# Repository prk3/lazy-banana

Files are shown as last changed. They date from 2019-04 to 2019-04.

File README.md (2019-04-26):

# About
Arduino Nano based controller for IKEA Bekant desk. Allows for manual height control, saving positions and auto height adjustment with a press of a button.

# Schematic
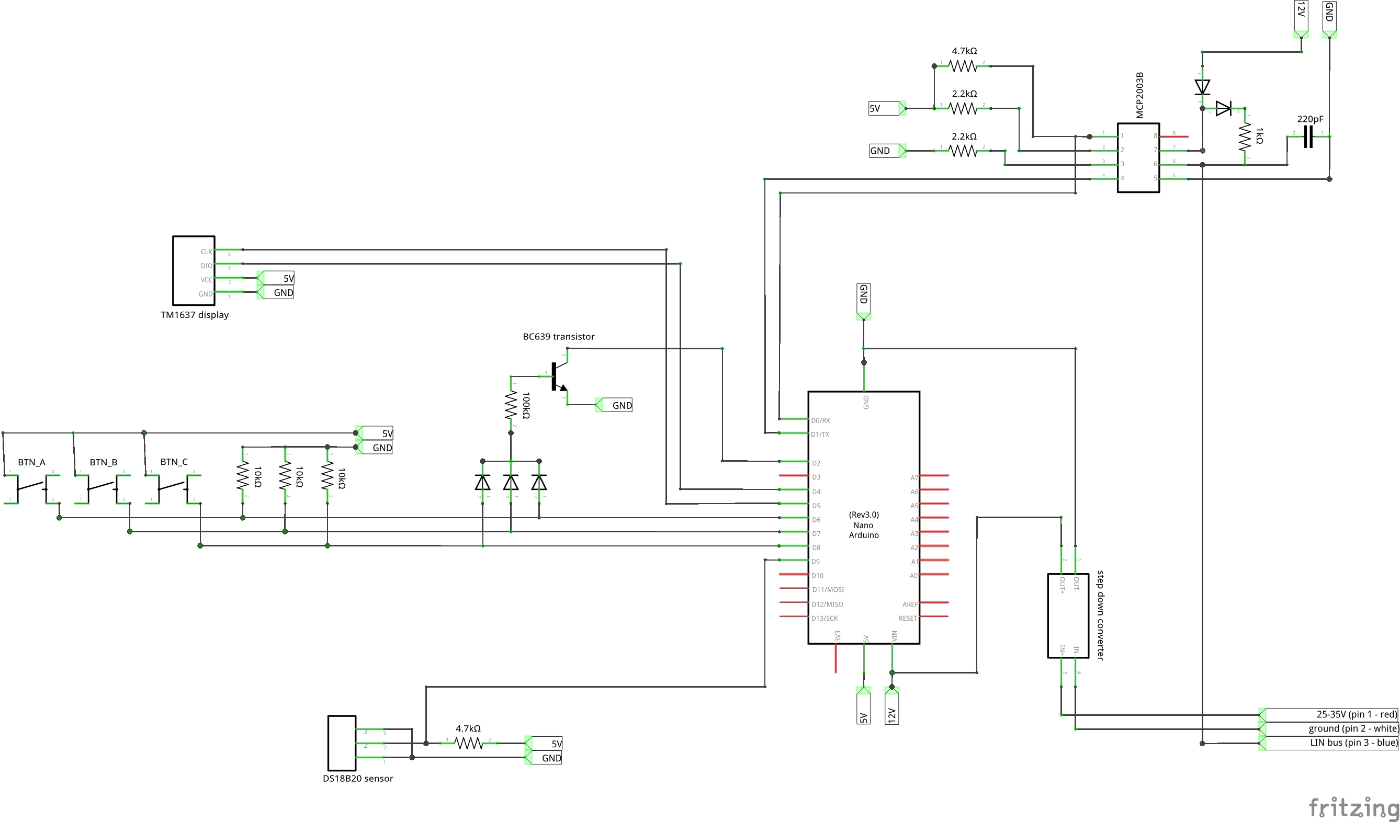
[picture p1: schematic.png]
Schematic

This schematic is a mix of trainman419's work, gcormier's improvements and my poor electronics skills. Please refer to the original in case you're uncertain about my schematic.

# Parts
| name | amount |
| --- | --- |
| Arduino nano clone - Atmega328, 16MHz, 5V | 1 |
| Step down converter LM2596S max 35V | 1 |
| 4-digit 7 segment display TM1637 | 1 |
| LIN interface/transceiver MCP2003B | 1 |
| temperature sensor DS18B20 | 1 |
| transistor BC639 | 1 |
| capacitor 220pF | 1 |
| diode 1N4148 | 5 |
| resistor 100k | 1 |
| resistor 10k | 3 |
| resistor 4.7k | 2 |
| resistor 2.2k | 2 |
| resistor 1k | 1 |

# Interface
Before testing auto-move, please factory reset the controller to initialize presets in EEPROM. You can do it by holding all three buttons on home screen.

- **SLEEP SCREEN**: Controller switches to this state after some time (15s by default) of inactivity. Press any button to wake up the controller and go to **home screen**.

- **HOME SCREEN**: Shows current height. Pressing buttons A-C will move desk to corresponding preset (**auto move screen**). Holding button A will redirect to **temperature screen**. Holding buttons B or C will redirect to **manual move screen**. Holding all three buttons will factory reset height presets.

- **TEMPERATURE SCREEN**: Shows temperature read from the Dallas sensor. Press any button to exit.

- **AUTO MOVE SCREEN**: Moves the desk to saved position. Press any button to cancel.

- **MANUAL MOVE SCREEN**: Holding B moves desk down, holding C moves desk up. Press button A to exit. Hold button A to save position (**save position screen**).

- **SAVE POSITION SCREEN**: Press button A, B or C to save position to preset 1, 2 or 3. Hold any button to cancel. 

# Code
Each part of controller's functionality is separated into `.cpp` + `.h` pair. All modules are then imported in `main.cpp` and used in a big state machine. Every state has it's id, initialization procedure and a handler (called every 50ms), which reacts to IO changes, performs some actions and redirects to a different state if needed.

All pins are configurable via const variables at the top of header files. Keep in mind that buttons work in INPUT mode and wake pin works in INPUT_PULLUP mode.

The code has been written in vscode with PlatformIO plugin. To make it work with Arduino IDE, move all files from `include`, `src` and `lib/gcormier_megadesk` to one folder named `main` and rename `main.cpp` file to `main.ino`. Make sure you have all dependencies installed.

# Dependencies
This project uses the following Arduino libraries:
1. OneWire - [https://github.com/PaulStoffregen/OneWire](https://github.com/PaulStoffregen/OneWire)
2. DallasTemperature - [https://github.com/milesburton/Arduino-Temperature-Control-Library.git](https://github.com/milesburton/Arduino-Temperature-Control-Library.git)
3. TM1637 [https://github.com/avishorp/TM1637.git](https://github.com/avishorp/TM1637.git)

# TODO
1. Add photos of the controller.
2. Model a case and 3d print it.
3. Record a demo.

# Issues
1. Auto move algorithm emulates UP/DOWN button pressing to reach target height. A better solution would be to keep desk in fine movement mode when it's close to target and slowly approach desired position.
2. Auto move algorithm isn't aware of desk's velocity. For this reason the desk refuses to move between presets that are very close to each other (controller thinks that desk is at full speed and would overshoot the target, thus it doesn't move at all).
3. Motors gradually slow down near min and max heights. This isn't handled by the controller and auto move undershoots targets near min and max.

# Credit
Big thanks to:
1. robin7331([IKEA-Hackant](https://github.com/robin7331/IKEA-Hackant/) project) for inspiring video and detailed explanation of desk's internals
2. trainman419 ([bekant](https://github.com/trainman419/bekant) project) for reproducing behavior of stock controller on Arduino
3. gcormier ([megadesk](https://github.com/gcormier/megadesk) project) for improvements to trainman419's schematic and code

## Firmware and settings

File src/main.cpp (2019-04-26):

#include <Arduino.h>
#include "buttons.h"
#include "display.h"
#include "temperature.h"
#include "desk.h"
#include "memory.h"
#include "state.h"
#include "sleep.h"

/**
 * Time after which controller goes to sleep.
 */
const uint16_t SLEEP_AFTER_S = 15;

unsigned long lastActivityTime = 0;

/**
 * The list of all program states.
 * It's a classic enum, because we want to avoid type errors.
 * ("states.h" doesn't know what states we'll have in the app)
 */
enum S: StateIdentifier {
    MAIN,
    AUTO_MOVE,
    MANUAL_MOVE,
    PRESET_CHOICE,
    PRESET_SAVE,
    FACTORY_RESET,
    TEMPERATURE,
    SLEEP,
};


// Each state requring data persistant across updates has it's own object.

struct {
    uint8_t preset = 0;
    uint16_t targetHeight = 0;
    bool forceStop = false;
    uint8_t finishedCount = 0;
} autoMoveData;

struct {
    uint8_t frame;
} infoStateData;

struct {
    uint8_t preset = 0;
} presetSaveData;

/**
 * Here we define how each state is initialized and handled in loop.
 */
const State states[] = {
    State {
        S::MAIN,
        []() {
            clearDisplayBuffer();
            drawIntegerInDisplayBuffer(getDeskHeight());
            sendBufferToDisplay();
        },
        [](StateChanger& changeState) {
            if (BTN_A.wasUnpressed()) {
                autoMoveData.preset = 0;
                return changeState(S::AUTO_MOVE);
            }
            if (BTN_B.wasUnpressed()) {
                autoMoveData.preset = 1;
                return changeState(S::AUTO_MOVE);
            }
            if (BTN_C.wasUnpressed()) {
                autoMoveData.preset = 2;
                return changeState(S::AUTO_MOVE);
            }

            if (!BTN_A.isPressed() && (BTN_B.wasHeld() || BTN_C.wasHeld())) {
                return changeState(S::MANUAL_MOVE, false);
            }

            if (BTN_A.wasHeld()) {
                if (BTN_B.isPressed() && BTN_C.isPressed()) {
                    return changeState(S::FACTORY_RESET);
                }

                return changeState(S::TEMPERATURE);
            }
        },
    },
    State {
        S::AUTO_MOVE,
        []() {
            autoMoveData.targetHeight = readPreset(autoMoveData.preset);
            autoMoveData.forceStop = false;
            autoMoveData.finishedCount = 0;
        },
        [](StateChanger& changeState) {
            clearDisplayBuffer();
            drawIntegerInDisplayBuffer(getDeskHeight());
            setColonInDisplayBuffer(true);
            sendBufferToDisplay();

            if (BTN_A.wasPressed() || BTN_B.wasPressed() || BTN_C.wasPressed()) {
                autoMoveData.forceStop = true;
            }

            // stops motors like if a button on the original controller was unpressed
            if (autoMoveData.forceStop) {
                if (!isDeskMoving()) {
                    return changeState(S::MAIN);
                }
                manualMoveLoop(ManualCommand::NONE);
            } else {
                // exit when "finished" reported 3 times
                if (!isDeskMoving() && ++autoMoveData.finishedCount > 3) {
                    return changeState(S::MAIN);
                }
                autoMoveLoop(autoMoveData.targetHeight);
            }
        },
    },
    State {
        S::MANUAL_MOVE,
        []() {},
        [](StateChanger& changeState) {
            clearDisplayBuffer();
            drawIntegerInDisplayBuffer(getDeskHeight());
            setColonInDisplayBuffer(true);
            sendBufferToDisplay();

            // change state only if desk is not moving
            if (!isDeskMoving()) {
                if (BTN_A.wasUnpressed()) {
                    return changeState(S::MAIN);
                }

                if (BTN_A.wasHeld()) {
                    return changeState(S::PRESET_CHOICE);
                }
            }

            if (!BTN_A.isPressed() && BTN_B.isPressed()  && !BTN_C.isPressed()) {
                manualMoveLoop(ManualCommand::DOWN);
            }
            else if (!BTN_A.isPressed() && !BTN_B.isPressed() && BTN_C.isPressed()) {
                manualMoveLoop(ManualCommand::UP);
            }
            else {
                manualMoveLoop(ManualCommand::NONE);
            }
        },
    },
    State {
        S::PRESET_CHOICE,
        []() {
            clearDisplayBuffer();
            drawIntegerInDisplayBuffer(123);
            displayBuffer[0] = CHAR_BARS;
            sendBufferToDisplay();
        },
        [](StateChanger& changeState) {
            if (BTN_A.wasUnpressed()) {
                presetSaveData.preset = 0;
                return changeState(S::PRESET_SAVE);
            }
            if (BTN_B.wasUnpressed()) {
                presetSaveData.preset = 1;
                return changeState(S::PRESET_SAVE);
            }
            if (BTN_C.wasUnpressed()) {
                presetSaveData.preset = 2;
                return changeState(S::PRESET_SAVE);
            }

            if (BTN_A.wasHeld() || BTN_B.wasHeld() || BTN_C.wasHeld()) {
                return changeState(S::MANUAL_MOVE);
            }
        },
    },
    State {
        S::PRESET_SAVE,
        []() {
            infoStateData.frame = 0;

            savePreset(presetSaveData.preset, getDeskArbitraryHeight());

            clearDisplayBuffer();
            displayBuffer[presetSaveData.preset + 1] = NUMBERS[presetSaveData.preset + 1];
            sendBufferToDisplay();
        },
        [](StateChanger& changeState) {
            if (++infoStateData.frame > 30) {
                return changeState(S::MAIN);
            }
        },
    },
    State {
        S::FACTORY_RESET,
        []() {
            infoStateData.frame = 0;

            savePreset(0, 400);
            savePreset(1, 6000);
            savePreset(2, 7000);

            clearDisplayBuffer();
            displayBuffer[0] = EMPTY;
            displayBuffer[1] = CHAR_F;
            displayBuffer[2] = CHAR_A;
            displayBuffer[3] = CHAR_C;
            sendBufferToDisplay();
        },
        [](StateChanger& changeState) {
            if (++infoStateData.frame > 30) {
                return changeState(S::MAIN);
            }
        },
    },
    State {
        S::TEMPERATURE,
        []() {
            // clear display
            clearDisplayBuffer();
            sendBufferToDisplay();

            // read temperature, round to 0.1
            float temp10 = getTemperature() * 10.0;
            float tempRounded = round(temp10) / 10.0;

            // display temperature, put ° symbol on 0.01 place
            drawFloatInDisplayBuffer(tempRounded);
            displayBuffer[3] = CHAR_DEGREE;
            sendBufferToDisplay();
        },
        [](StateChanger& changeState) {
            if (BTN_A.wasPressed() || BTN_B.wasPressed() || BTN_C.wasPressed()) {
                return changeState(S::MAIN);
            }
        },
    },
    State {
        S::SLEEP,
        []() {
            clearDisplayBuffer();
            sendBufferToDisplay();
        },
        [](StateChanger& changeState) {
            sleep();
            lastActivityTime = millis();
            return changeState(S::MAIN);
        },
    },
};

/**
 * Returns pointer to state given state id.
 */
const State *findState(StateIdentifier id) {
    for (const State& state: states) {
        if (state.id == id) {
            return &state;
        }
    }
    return nullptr;
}

const State *currentState;


/**
 * Disable unused peripherals, initialize all modules, start the state machine.
 */
void setup() {
    // http://www.fiz-ix.com/2012/11/save-power-by-disabling-arduino-peripherals/
    // please comment out the following 3 lines if you need analog pins
    ADCSRA = ADCSRA & B01111111;
    ACSR = B10000000;
    DIDR0 = DIDR0 | B00111111;

    setupSleep();
    setupButtons();
    setupDisplay();
    setupTemperature();
    setupDesk();

    forgetButtons();
    currentState = findState(S::MAIN);
    currentState->initialize();
}

/**
 * Handle current state, change state if requested, read buttons, check sleep condition.
 * Repeat every 50ms ===FOREVER=== 😱.
 */
void loop() {

    StateChanger changer;
    currentState->handle(changer);
    delay(50);

    if (changer.wasChanged()) {
        const State* newState = findState(changer.newState());
        if (newState) {
            if (changer.wereButtonsForgotten()) {
                forgetButtons();
            }
            currentState = newState;
            currentState->initialize();
        }
    }

    updateButtons();

    // check if controller should go to sleep
    unsigned long now = millis();

    if (isDeskMoving() || BTN_A.isPressed() || BTN_B.isPressed() || BTN_C.isPressed()) {
        lastActivityTime = now;
    } else {
        if (lastActivityTime > now) {
            lastActivityTime = 0;
        }
        if (now - lastActivityTime >= SLEEP_AFTER_S * 1000UL) {
            const State *sleepState = findState(S::SLEEP);
            if (sleepState) {
                currentState = sleepState;
                currentState->initialize();
            }
        }
    }
}

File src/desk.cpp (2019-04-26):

#include "desk.h"
#include "lin.h"

// this file is a big cherry pick of gcormier/megadesk/Code/megadesk.ino
// the code has been reformated, refactored and cut down to only handle desk movement
// check out lib/gcormier_megadesk/LICENSE


/////////////////////////////////////////// private

#define FINE_MOVEMENT_VALUE   100 // Based on protocol decoding

#define LIN_CMD_IDLE          252
#define LIN_CMD_RAISE         134
#define LIN_CMD_LOWER         133
#define LIN_CMD_FINE          135
#define LIN_CMD_FINISH        132
#define LIN_CMD_PREMOVE       196

#define LIN_MOTOR_BUSY        2
#define LIN_MOTOR_BUSY_FINE   3

// idle code, different value for different desk variants
// smaller Bekant variant: 96
// bigger Bekant variant: 0
const uint8_t LIN_MOTOR_IDLE = 96;

// values of 4 constants below depend on moveLoop calling frequency and load on your desk
// please adjust these values if you experience auto move overshooting/undershotting

// distance the desk is expected to travel between moveLoop function calls when moving UP
// in my case it's between 42 and 45
const uint16_t DISTANCE_UP_PER_UPDATE = 43;

// distance the desk is expected to travel between moveLoop function calls when moving DOWN
// in my case between 39 and 42
const uint16_t DISTANCE_DOWN_PER_UPDATE = 40;

// distance the desk travels after unpressing UP button, in Bekant's height units
// in my case between 78 and 84
const uint16_t BRAKING_UP_DISTANCE = 81;

// distance the desk travels after unpressing DOWN button, in Bekant's height units
// in my case between 87 and 93
const uint16_t BRAKING_DOWN_DISTANCE = 90;


// Changing these might be a really bad idea. They are sourced from
// decoding the OEM controller limits. If you really need a bit of extra travel
// you can fiddle with SAFETY, it's an extra buffer of a few units.
const uint16_t SAFETY = 20;
const uint16_t DANGER_MAX_HEIGHT = 6777 - SAFETY;
const uint16_t DANGER_MIN_HEIGHT = 162 + SAFETY;

enum class DeskState: uint8_t {
    OFF,
    STARTING,
    UP,
    DOWN,
    STOPPING1,
    STOPPING2,
    STOPPING3,
    STOPPING4,
};

enum class MoveDirection: uint8_t {
    UP,
    DOWN,
    NONE,
};

struct MoveLoopData {
    uint16_t enc_a;
    uint16_t enc_b;
    uint16_t enc_target;
};

struct DeskData {
    DeskState state;
    MoveDirection direction;
    uint16_t height;
    bool motorsIdling;
};

DeskData deskData {
    DeskState::OFF,
    MoveDirection::NONE,
    DANGER_MIN_HEIGHT,
    true,
};

Lin lin(Serial, TX_PIN);

unsigned long t = 0;

void delay_until(unsigned long ms) {
    unsigned long end = t + (1000 * ms);
    unsigned long d = end - micros();

    // crazy long delay; probably negative wrap-around
    // just return
    if (d > 1000000) {
        t = micros();
        return;
    }

    if (d > 15000) {
        unsigned long d2 = (d-15000) / 1000;
        delay(d2);
        d = end - micros();
    }
    delayMicroseconds(d);
    t = end;
}

template <typename T>
T difference(T a, T b) {
    return a > b ? a - b : b - a;
}

// Really weird startup sequence, sourced from the controller.
void linInit() {
    uint8_t resp[8];

    auto sendInitPacket = [&resp](uint8_t a1 = 255, uint8_t a2 = 255, uint8_t a3 = 255, uint8_t a4 = 255) {
        uint8_t packet[8] = { a1, a2, a3, a4, 255, 255, 255, 255 };

        // Custom checksum formula for the initialization
        int chksum = a1 + a2 + a3 + a4;
        chksum = chksum % 255;
        chksum = 255 - chksum;

        lin.send(60, packet, 8, 2, chksum);
        delay(3);
        return lin.recv(61, resp, 8, 2);
    };

    // Brief stabilization delay
    delay(150);

    sendInitPacket(255, 7);
    sendInitPacket(255, 7);
    sendInitPacket(255, 1, 7);
    sendInitPacket(208, 2, 7);

    uint8_t initA;
    for (initA = 0; sendInitPacket(initA, 2, 7) == 0; initA++) {}

    sendInitPacket(initA, 6,  9, 0);
    sendInitPacket(initA, 6, 12, 0);
    sendInitPacket(initA, 6, 13, 0);
    sendInitPacket(initA, 6, 10, 0);
    sendInitPacket(initA, 6, 11, 0);
    sendInitPacket(initA, 4,  0, 0);

    uint8_t initB;
    for (initB = initA + 1; sendInitPacket(initB, 2, 0, 0) == 0; initB++) {}

    sendInitPacket(initB, 6,  9, 0);
    sendInitPacket(initB, 6, 12, 0);
    sendInitPacket(initB, 6, 13, 0);
    sendInitPacket(initB, 6, 10, 0);
    sendInitPacket(initB, 6, 11, 0);
    sendInitPacket(initB, 4,  1, 0);

    for (uint8_t initC = initB + 1; initC < 8; initC++) {
        sendInitPacket(initC, 2, 1, 0);
    }

    sendInitPacket(208, 1, 7, 0);
    sendInitPacket(208, 2, 7, 0);

    delay(15);

    uint8_t magicPacket[3] = { 246, 255, 191 };
    lin.send(18, magicPacket, 3, 2);

    delay(5);
}

void readDeskData(MoveLoopData &loopData) {
    uint8_t empty[3] = { 0, 0, 0 };
    uint8_t node_a[4] = { 0, 0, 0, 0 };
    uint8_t node_b[4] = { 0, 0, 0, 0 };

    // Send PID 17
    lin.send(17, empty, 3, 2);
    delay_until(5);

    // Recv from PID 09
    lin.recv(9, node_b, 3, 2);
    delay_until(5);

    // Recv from PID 08
    lin.recv(8, node_a, 3, 2);
    delay_until(5);

    // Send PID 16, 6 times
    for (uint8_t i = 0; i < 6; i++) {
        lin.send(16, 0, 0, 2);
        delay_until(5);
    }

    // Send PID 1
    lin.send(1, 0, 0, 2);
    delay_until(5);

    loopData.enc_a = node_a[0] | (node_a[1] << 8);
    loopData.enc_b = node_b[0] | (node_b[1] << 8);
    loopData.enc_target = loopData.enc_a;

    deskData.height = loopData.enc_a;
    deskData.motorsIdling = node_a[2] == LIN_MOTOR_IDLE && node_b[2] == LIN_MOTOR_IDLE;
}
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
